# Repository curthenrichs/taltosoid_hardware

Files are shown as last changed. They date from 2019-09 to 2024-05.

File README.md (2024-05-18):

# taltosoid_srf
Taltos-oid seeks to understand the practicality in augmenting the human body with an additional robotic finger for everyday tasks. Taltos translates to shaman from Hungarian mythology. One potential defining trait of a shaman in the mythos is physical abnormalities such as an additional finger. Ergo Taltos-oid is using robotics to create a shaman through robotics (or just to help stabilize coffee cups).

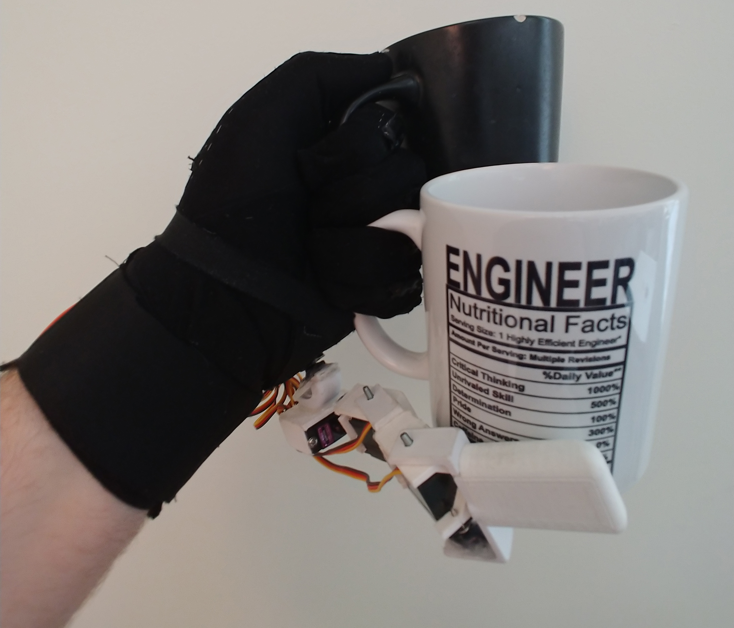
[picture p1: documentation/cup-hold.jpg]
Picture shows a gloved hand holding a cup with thumb, index finger, and middle finger. A second cup is being held with the ring finger, pinky, and the supernumerary robotic opposable finger


## Motivation
I have been fascinated with augmenting the human body with robotic limbs for years now. Nearly as long as I have been introduced to the concepts of transhumanism and post-humanism. There is something captivating about the question "what would be different about me if I were not human". My first attempt at extending human ability is to develop a supernumerary robotic finger that can be used to assist and augment the wearer in grasping tasks during daily living.

There are two schools of thought regarding the "agent-status" of the robotic finger. One view is to treat the robotic finger as a pass-through device extracting signals from EMG or finger tracking without any cognitive processes performed by the finger. This system relies on expertise of the wearer to control the device for the given task. The alternate view is to endow decision making onto the finger, in effect treating it as a traditional robotic agent and thus casting the control problem as social human-robot collaboration. I believe the second view is where the most impact with such a device can be found. (This project will explore both since the first view is much easier to get started with).

## Design
I aim to capture the general hardware and software decisions made. Each section will break down the discussion by version (at this time only version one).

### Hardware

#### Version One
The hardware design can be broken into three subsystems:
- Robotic Finger
- Resistive Sense Glove
- Controller Wrist Strap

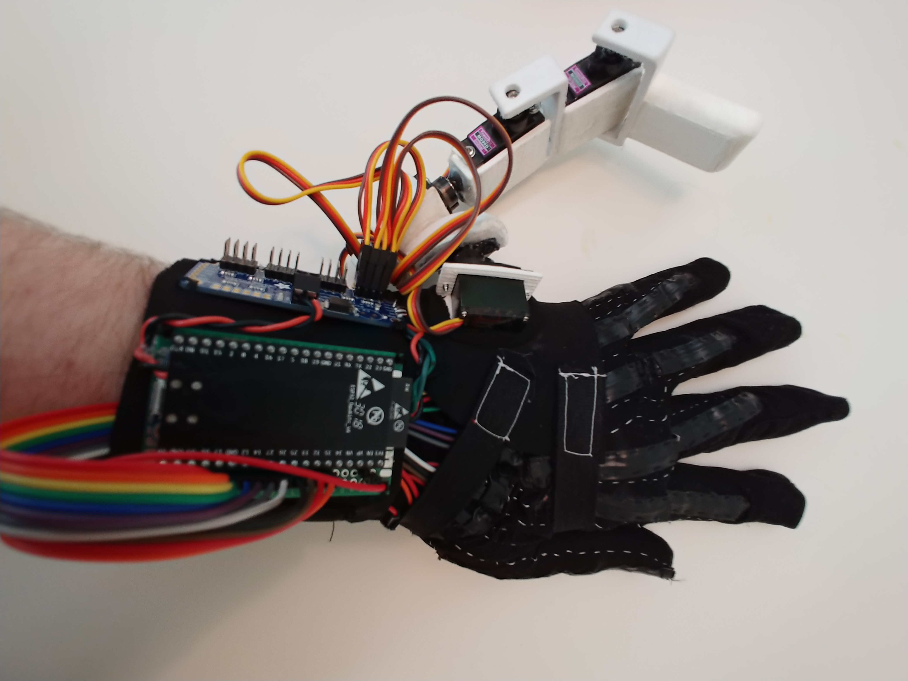
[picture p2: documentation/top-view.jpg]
Picture shows a gloved hand with the robotic finger attached. Control board (ESP32) is also shown. Version one hardware


**Robotic Finger**:
I designed a 3D printed robotic finger that uses high-torque micro servos to direct drive the joints. This design was primarily done for proof of concept. I suggest that future versions use some kind of linkage in order to keep the weight of the finger at the base. As it currently is, the servos don't have enough torque to hold even medium weighted objects. 

**Resistive Sense Glove**:
For version one I went with a simple-direct control strategy. In order to accomplish this I developed home-made flex sensors and sewed them onto a glove-liner. The sensors were made from two thick conductive threads with flexible resisitive material in between. I then used conductive copper fabric on each end as connective tabs. I covered the copper with conductive paint to adhere the conductive thread with the copper. Lastly, I sewwed thinner conductive thread down the glove to headerpins, again adhering with conductive paint and electrical tape. 

I later discovered while using the glove that sweat breaks down the conductive paint causing intermittent connections. I suggest future designs not use the approach described above. Instead it will be much more reliable to use off-the-shelf flex sensors even if they are less comfortable to wear. 

**Controller Wrist Strap**:
I build the controller wrist strap to physically keep the glove and finger aligned. Specifically, the wrist strap limits the glove from shifting around whent the user is moving their hand. Unfortuntely this makes it a bit uncomfortable to wear as it can get rather tight.

Electronically, the finger servos connect into a servo control board and the resistive sensors connect into an analog mux. The brains of the system is an ESP32 with arduino firmware. I also mounted an IMU at one point though later removed it for a different project.

**Improvement**:
Below are some of the key improvements needed for version two:

- Improved power system
- Custom, compact controller PCB
- Higher torque, more compact finger design

### Software

#### Version One
Version one software has a PC component and the low-level firmware. The PC was responsible for training and executing an ML model that mapped finger flex sensor input into appropriate joint control. The firmware acted as a relay. It captured low-level ADC voltage readings from the flex sensors. It provided direct joint-control to each joint. And it provided IMU readings. Communication was done over WiFi (thanks to the ESP32's capabilities).

I also started developing a ROS layer for this device, partially as a learning exercise and equally as the next step of building verison two. My goal is to build out several control strategies in simulation while working on a good second finger design.

Below are some of the key improvements needed for version two:

- Explore alternative methods for user control (EMG, nIRS, Vision)
- Communication from finger back to wearer (haptic?, animation?)
- Environment sensing (3D grasp targeting)
- Collision avoidance, context aware pose
- Augmentaton control strategies
- (Recently added) LLM control
- Tamagotchi mode

## Experiments
My goal once I develop version two is to perform a day-long autobiographical study wearing the finger. Work can also be done under more strict laboratory experiments investigating grasping tasks.

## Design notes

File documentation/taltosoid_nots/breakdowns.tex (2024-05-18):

I put my finger on today as I am restarting the project and wanted to remind myself of the wearability. First as I type, my wrist  wrests awkwardly, this is due to the mounting point of the finger. Second blood circulation at my thumb and index finger are not great due to the mounting Velcro straps to hold the flex sensors. The sensors themselves dig into my skin at the finger tips and at the base. Most prominent is the digging in on the index finger. As I wear the device the compute strap has a wire under that digs in as well. 

The finger mounting point is awkward to type on a keyboard and the sensor mounting makes it awkward to type on a phone. Taking pictures of the hand is also difficult. 

I am also not pleased with the Velcro finger straps removing sensation on the finger tips (often the straps make contact with the grasped object first). I also am not a fan of the open wires (and more generally the bulk) of the compute module on the wrist. Note too that this is without batter which adds considerable weight. 

The finger itself is worn and would need considerable rework if I go that route. I advise we continue to use the current finger, but rethink the control electronics.

What is my budget for this? \$ 100 for version 1.2. + the a couple hundred for version 2?

I think we ought to make a new glove thing and rework the current compute module for version 1.2. The underlying hardware is probably fine for an early evaluation provided I fix the comfort issues. Version 2 should have a better scheme for mounting the finger.

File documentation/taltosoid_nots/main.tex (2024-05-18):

%%%%%%%%%%%%%%%%%%%%%%%%%%%%%%%%%%%%%%%%%%%%%%%%%%%%%%%%%%%%%%%%%%%%%%%%%%%%%%%%
%2345678901234567890123456789012345678901234567890123456789012345678901234567890
%        1         2         3         4         5         6         7         8

\documentclass[letterpaper, 10 pt, conference]{ieeeconf}  % Comment this line out if you need a4paper

%\documentclass[a4paper, 10pt, conference]{ieeeconf}      % Use this line for a4 paper

\IEEEoverridecommandlockouts                              % This command is only needed if 
                                                          % you want to use the \thanks command

\overrideIEEEmargins                                      % Needed to meet printer requirements.

%In case you encounter the following error:
%Error 1010 The PDF file may be corrupt (unable to open PDF file) OR
%Error 1000 An error occurred while parsing a contents stream. Unable to analyze the PDF file.
%This is a known problem with pdfLaTeX conversion filter. The file cannot be opened with acrobat reader
%Please use one of the alternatives below to circumvent this error by uncommenting one or the other
%\pdfobjcompresslevel=0
%\pdfminorversion=4

% See the \addtolength command later in the file to balance the column lengths
% on the last page of the document

% The following packages can be found on http:\\www.ctan.org
%\usepackage{graphics} % for pdf, bitmapped graphics files
%\usepackage{epsfig} % for postscript graphics files
%\usepackage{mathptmx} % assumes new font selection scheme installed
%\usepackage{times} % assumes new font selection scheme installed
%\usepackage{amsmath} % assumes amsmath package installed
%\usepackage{amssymb}  % assumes amsmath package installed

\begin{document}

\title{\LARGE \bf Exploration of a Wearable Supernumerary Finger as Embodied Robotic Companion: An Autobiographical Case Study}

\author{Curt Henrichs}

% My goal is to write a short (4-page) paper regarding this topic

\maketitle
\thispagestyle{empty}
\pagestyle{empty}

\begin{abstract}

\end{abstract}

\section{Introduction}

The relationship between an agent and its environment informs both form(s) and function(s) it takes. Agents able to successfully operate within their environment have a high "fitness". For robotics, designers often have to consider the degree of structure provided within the environment; the proximity and relationship with humans the robot may encounter; and the task/role the it ought to perform. In human-robot interaction scenarios, a "fit" robot is often one that can successfully navigate the vagaries of human behavior. 

Wearable robots pose an interesting space to explore this "fitness" design task. Most prominently, wearable robots exist within the intimate social zone of their wearer during use and thus are enmeshed within the lives of their wearer. For example, this affords the robot access to observe and act during social interactions between the wearer and third-party agents. The designer also needs to consider casting the wearable agent as independent versus an extension of the wearer. This choice informs the set of behaviors a robot ought to perform. A wearer will expect independent behavior from a wearable tele-presence robot, but less so a prosthetic. The environments that a wearable robot will find itself in is as unstructured as the human wearer's. This could pose challenges if the robot's goal requires recognizing and manipulating objects with an end-effector. Even the proper mounting of wearable robots on the wearer's body during manipulation poses challenges to the designer.

In this paper, we focus on a specific subset of wearable robotics used to augment hand functionality, called supernumerary robotic fingers\footnote{Part of the broader set of supernumerary robotic limbs.}. We built a prototype system--\textit{Taltosoid}--designed to act as an embodied, artificial pet; inspired by popularized virtual pets (e.g., Tamagotchis). This work aims to explore the design of such a system. We discuss our findings through several self-experimentation case studies culminating with a proposal on future directions necessary to develop a robust taxonomy of the design space.

Our contributions are:
\begin{itemize}
    \item Design and implementation of a prototype embodied, artificial pet supernumerary robotic finger (\textit{Taltosoid});
    \item Case studies exploring usability and functionality of \textit{Taltosoid} through self-experimentation.
\end{itemize}

\section{Background}

\subsection{Supernumerary Fingers}

\subsection{Robot Companions}

\subsection{Design Space}

% Introduce Taltosoid here

\section{Method \& Design}
To design a compelling interaction between the wearer and finger, we conducted a preliminary autobiographical evaluation. The purpose of this evaluation is to understand what the wearer's common activities are and capture initial breakdowns whilst wearing the hardware. We then designed an embodied companion system running on the hardware. We showcase the functionality of the companion with several formative case studies drawn from a day-long autobiographical session. See each subsection for further discussion.

\subsection{Day in the Life of a Wearer}
Our goal is to understand a wearer's common activities--specifically how they use their hands---throughout a typical day. Furthermore, we want to capture the long-term use breakdowns of the current hardware prototype. This necessitates intrusive entry into the life of the wearer. Hence, we opt for an autobiographical design approach were researchers are framed as the the target user; thus performing the evaluation. We discuss the literature and limitations of this approach in the discussion section. The researcher (we) performed a two-day evaluation, with day one dedicated to tracking typical hand use and day two focused on wearing a supernumerary robotic finger in a limited actuation mode. 

During the day, we wore a camera mounted on the left shoulder facing forward and down to capture a top-down view of the activities. We also mounted a camera on our lower arm to further capture hand activity. For day two we also wore the hardware in a limited actuation mode. In this mode, the device used two flex sensors mounted on the researchers index finger and thumb to guide thumb position using a simple heuristic. 

The evaluation day was considered started after we started recording. We started wearing the cameras as soon as we woke up. The day ended when we went to bed; stopping recording and taking off the cameras. During the day, when a camera's battery became critically low, we would stop recording and switch out batteries. We did not consider this part of ``daily-life activities'' and thus disregard it from coding and analysis.

All video data was then coded for hand activity themes and wearability breakdowns following a grounded theory approach. After the 

\textit{Day One - A typical day -}

\textit{Day Two - Wearing the prototype -}

% Purpose is to understand the weare's common activites and capture initial breakdowns

\subsection{Designing the Embodied Companion}

\subsection{Case Studies}
Following the same protocol as our first evaluation, we performed a day-long usability evaluation of the hardware + embodied companion. We wore cameras on both the shoulder and lower arm. We coded the video data for hand activity and wearability breakdowns. 

\textit{Day Three - Wearing the companion - }

\subsubsection{Case 1}

\subsubsection{Case 2}

\subsubsection{Case 3}

\section{Discussion}

% autobiographical research, the good/bad/and ugly

\end{document}

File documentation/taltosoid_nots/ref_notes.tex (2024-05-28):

\section{Notes}

Why is situating a robot onto the human body an interesting and worthwhile project to explore?
- Passive vs active agent problem
    - Smart prosthetic are effectively passive agents mapping human input directly to an actuation state.
    - A social robot is an active agent separate from the self. We ascribe it motive and observe its actuation. 
    - Wearable robots could blend the line between these switching between active and passive robot states
- Robots situated on the human body live near-exclusively in the intimate social zone while in operation.
    - As such we expect interesting social breakdowns (if we cast this an active agent problem)
        - When should the robot engage in an activity? 
    - Do we gender the robot (and what are the users preferences there). Do we explore the sexual orientation of the robotic finger (if again treated as a multi-agent problem)
- Situated on the body offers access to the life of the user as they perform daily tasks
    - More importantly it affords affecting state in addition to gathering it
    - Cell-phones and wearables like smart bands/watches and eye wear approach this. It resolves the sensing (and in a limited case actuation ~ Holograms).
- How do these devices effect lifestyle e.g., clothing choice (style-design and accommodations). 
    - Would users be interested in making these modifications for an external agent
- Future is trans-human?

********* Human-robot proxemics: physical and psychological distancing in human-robot interaction - https://dl.acm.org/doi/abs/10.1145/1957656.1957786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

Persuasive Robotics: The influence of robot gender on human behavior - https://ieeexplore.ieee.org/document/5354116

Why Not Marry a Robot? - https://link.springer.com/chapter/10.1007/978-3-319-57738-8_1

Gendering Humanoid Robots: Robo-Sexism in Japan - https://journals.sagepub.com/doi/abs/10.1177/1357034x10364767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

Can you Tell the Robot by the Voice? An Exploratory Study on the Role of Voice in the Perception of Robots - https://ieeexplore.ieee.org/abstract/document/8673305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

Gendered robot voices influencing trust -
towards a robot recommendation system
 - https://webapps.cs.umu.se/uminf/reports/2020/001/part1.pdf#page=7

‘Robot Kung fu’: Gender and professional identity in biology and philosophy reviews - https://www.sciencedirect.com/science/article/abs/pii/S0378216607000161

Gendered voice and robot entities: Perceptions and reactions of male and female subjects - https://ieeexplore.ieee.org/abstract/document/5354204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

Is Your Roomba Male or Female? The Role of Gender Stereotypes and Cultural Norms in Robot Design - https://ojs.stanford.edu/ojs/index.php/intersect/article/view/171

The Philosophical Case for Robot Friendship - https://www.jstor.org/stable/10.5325/jpoststud.3.1.0005

When stereotypes meet robots: The double-edge sword of robot gender and personality in human–robot interaction - https://www.sciencedirect.com/science/article/pii/S0747563214002921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

Why supernumarary robotic fingers? What benefits to society does this confer? 

How do we gamify the pet finger process - (and why)? 
- Voluntary compliance / building habits (wearable fingers are not a well understood phenomena for the average wearer)
- Long-term study potential

Does Gamification Work? -- A Literature Review of Empirical Studies on Gamification - https://ieeexplore.ieee.org/abstract/document/6758978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

Tamagotchis need not die — Verification of statemate designs - https://link.springer.com/chapter/10.1007/BFb0054174

Virtual Pet Game Application to Train and Manage How to Raise a Cat Well and Properly - https://ieeexplore.ieee.org/abstract/document/9339682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

Disposable Love: The Rise and Fall of a Virtual Pet - https://journals.sagepub.com/doi/abs/10.1177/14614449922225591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

3D Virtual Pet Multiplayer Game Dengan Menggunakan Google Cardboard - https://repository.its.ac.id/75819/

Virtual Pet: Trends of Development - https://link.springer.com/chapter/10.1007/978-3-030-37737-3_47

Bouncy: An Interactive Life-Like Pet - https://citeseerx.ist.psu.edu/viewdoc/download?doi=10.1.1.24.6293&rep=rep1&type=pdf

Design and implementation of an educational virtual pet using the OCC theory - https://link.springer.com/article/10.1007/s12652-011-0089-4

A study of integrating social networking service into the virtual pet web game system - https://ieeexplore.ieee.org/abstract/document/6765475

Developing a believable interactive agent using
virtual pet design - http://tombattey.com/wp-content/uploads/2019/09/Developing-a-believable-interactive-agent-using-virtual-pet-design.pdf

Pretty Pelvis: A Virtual Pet Application That Breaks Sedentary Time by Promoting Gestural Interaction - https://dl.acm.org/doi/abs/10.1145/2702613.2732807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

AIBO: Toward the Era of Digital Creatures - https://journals.sagepub.com/doi/abs/10.1177/02783640122068092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

Loving a virtual pet: Steps toward the technological erosion of emotion - https://www.proquest.com/docview/200590681?pq-origsite=gscholar&fromopenview=true

Methodology
A Self-Guiding Tool to Conduct Research With Embodiment Technologies Responsibly - https://internal-journal.frontiersin.org/articles/10.3389/frobt.2020.00022/full

self-experimentation / autobiographical

Revealing Tensions in Autobiographical Design in HCI - https://dl.acm.org/doi/abs/10.1145/3196709.3196781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

Autobiographical design in HCI research: designing and learning through use-it-yourself - https://dl.acm.org/doi/abs/10.1145/2317956.2318034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

A Sample of One: First-Person Research Methods in HCI - https://dl.acm.org/doi/abs/10.1145/3301019.3319996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

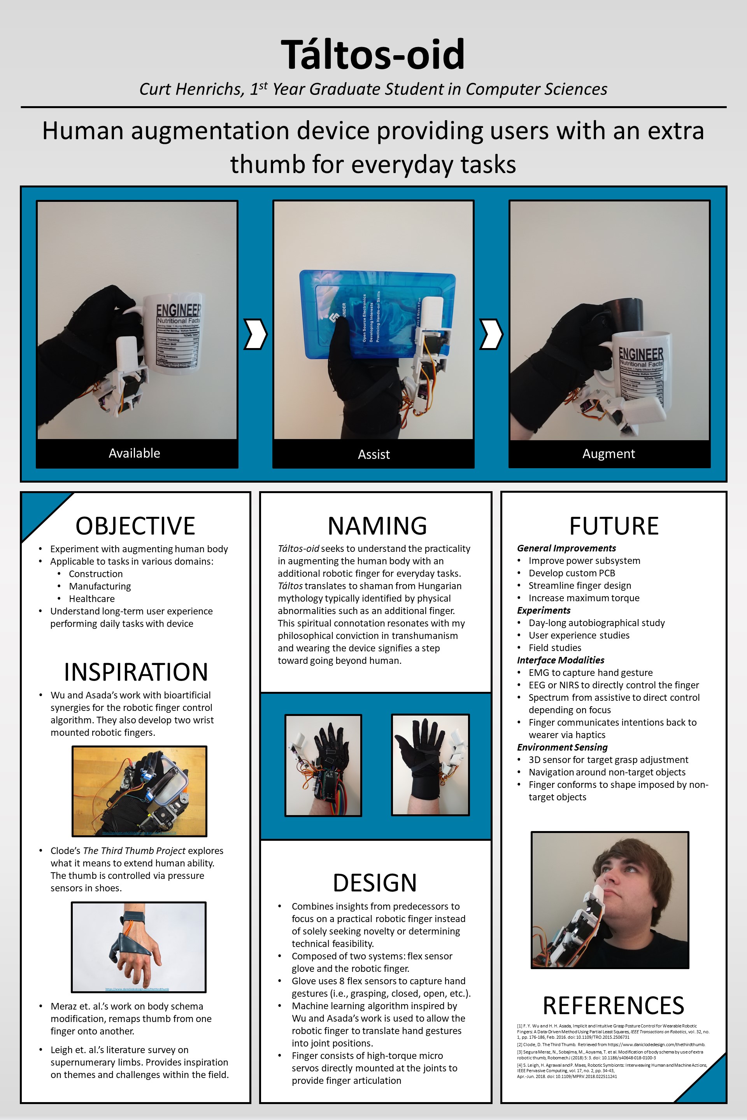
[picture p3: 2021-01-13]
documentation/Poster.jpg

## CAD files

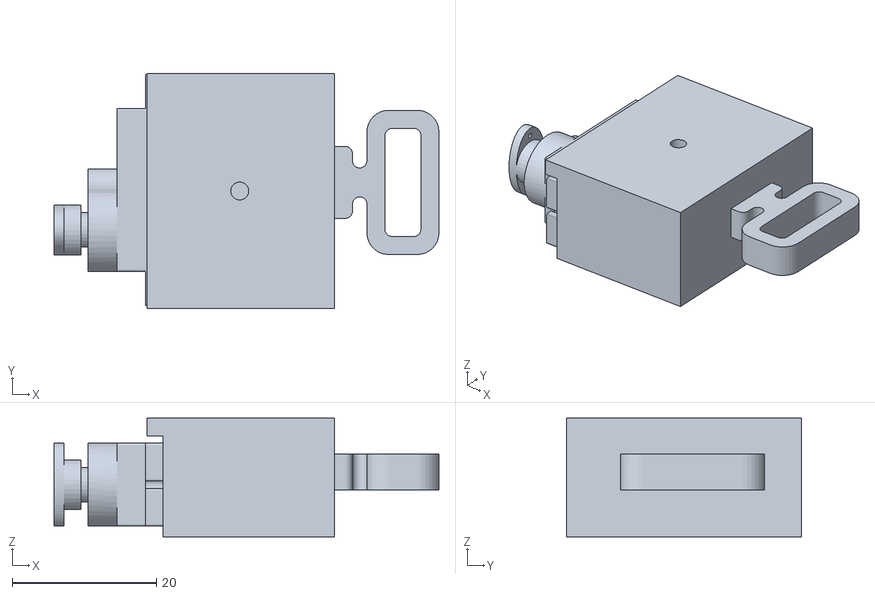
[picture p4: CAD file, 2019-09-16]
taltosoid_driver/description/meshes/rotation_root.stl
53.4 x 32.6 x 16.5

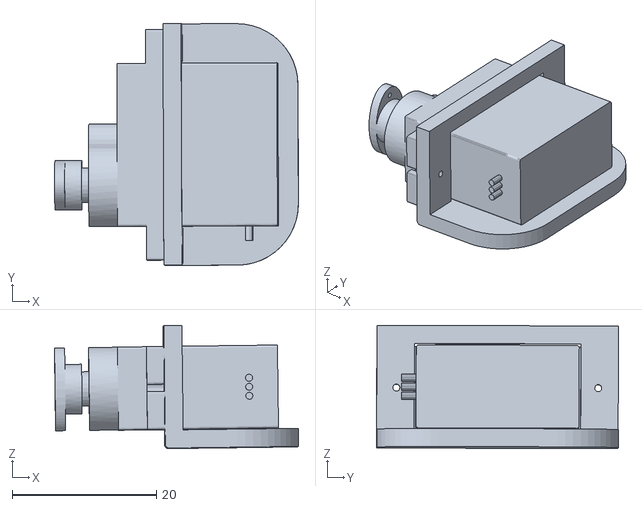
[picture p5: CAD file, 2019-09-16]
taltosoid_driver/description/meshes/finger_root.stl
33.9 x 33.6 x 17.1

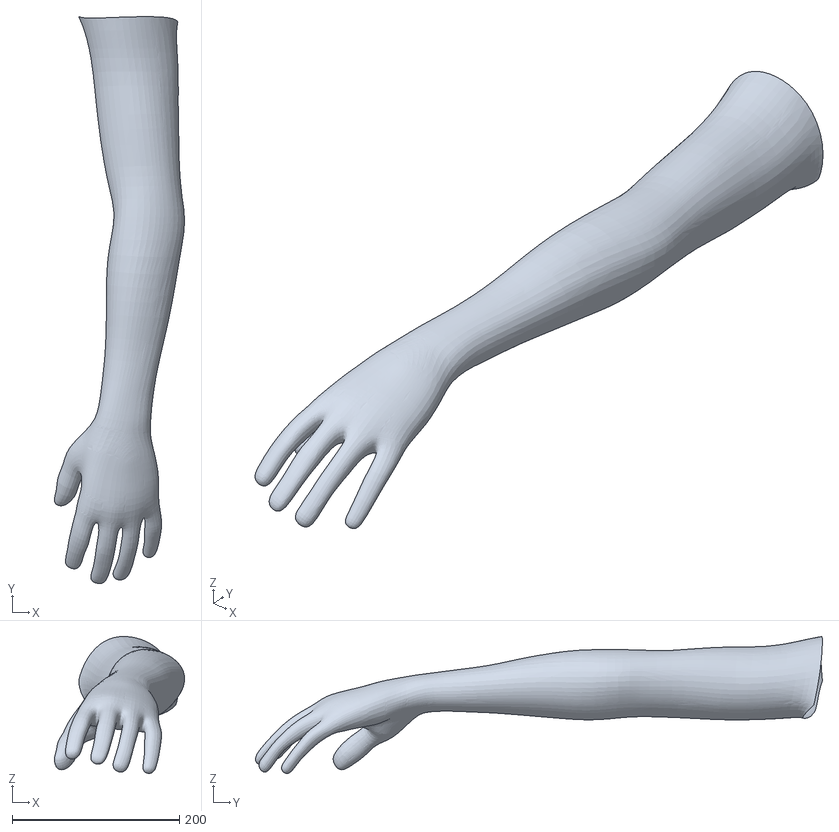
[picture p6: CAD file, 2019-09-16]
taltosoid_driver/description/meshes/hand.stl
155.7 x 678.1 x 163.9

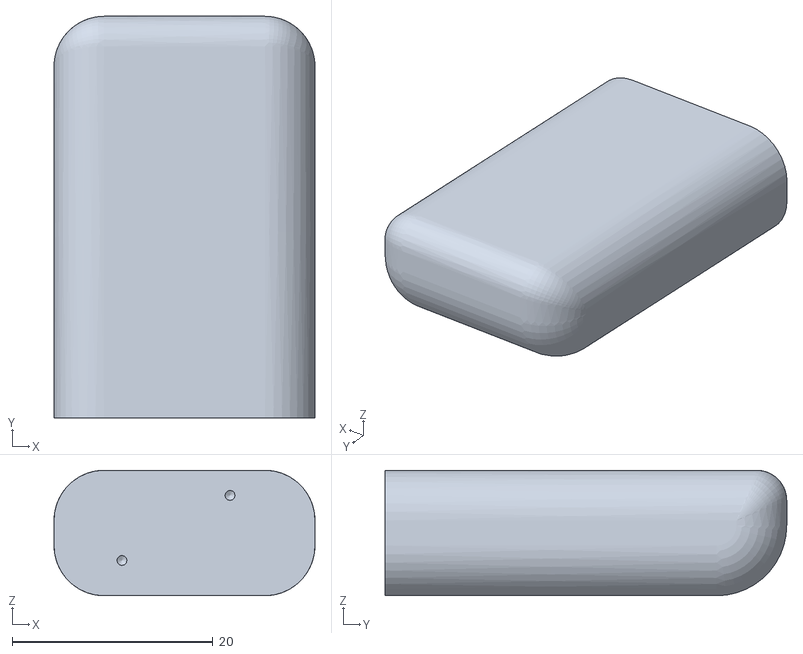
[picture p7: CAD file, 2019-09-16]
taltosoid_driver/description/meshes/finger_tip.stl
26.0 x 40.0 x 12.5

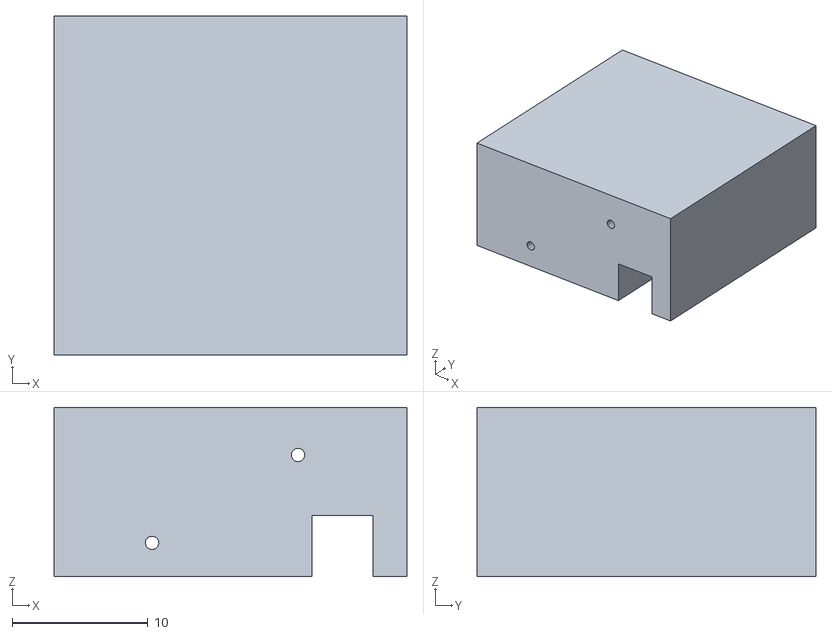
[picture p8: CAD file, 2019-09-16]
taltosoid_driver/description/meshes/spacer.stl
26.0 x 25.0 x 12.5

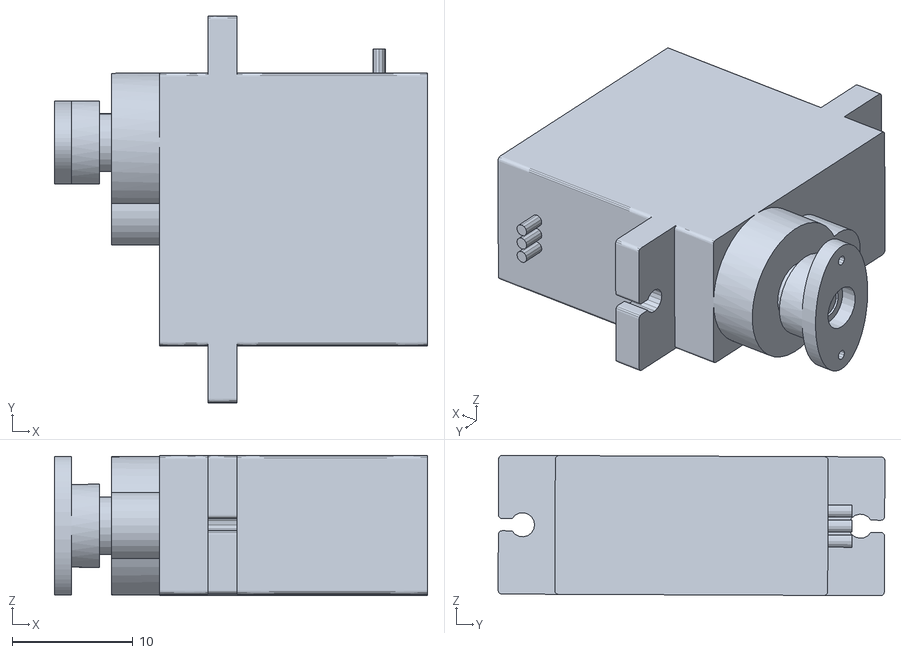
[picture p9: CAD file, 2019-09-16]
taltosoid_driver/description/meshes/servo.stl
30.9 x 32.1 x 11.6

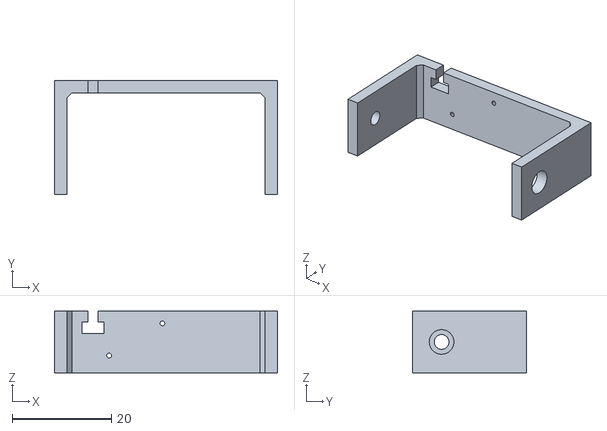
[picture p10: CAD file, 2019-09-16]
taltosoid_driver/description/meshes/finger_hinge.stl
45.0 x 23.0 x 12.5

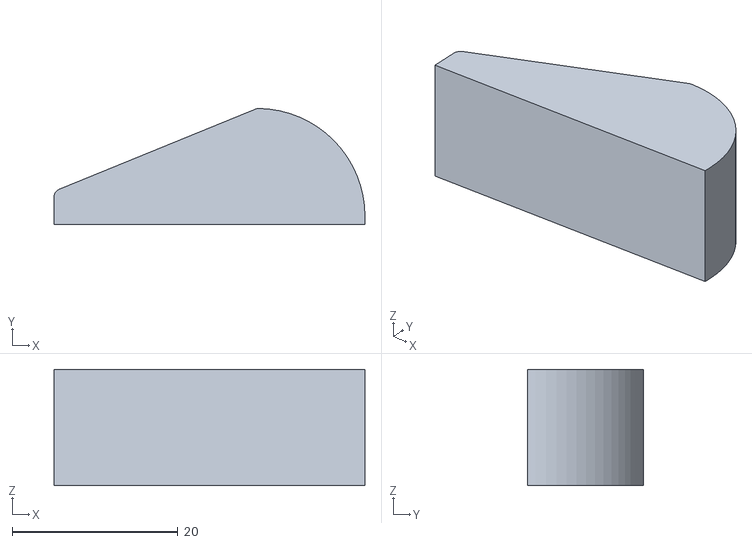
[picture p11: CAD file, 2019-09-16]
taltosoid_driver/description/meshes/base_spacer.stl
37.5 x 14.0 x 14.0

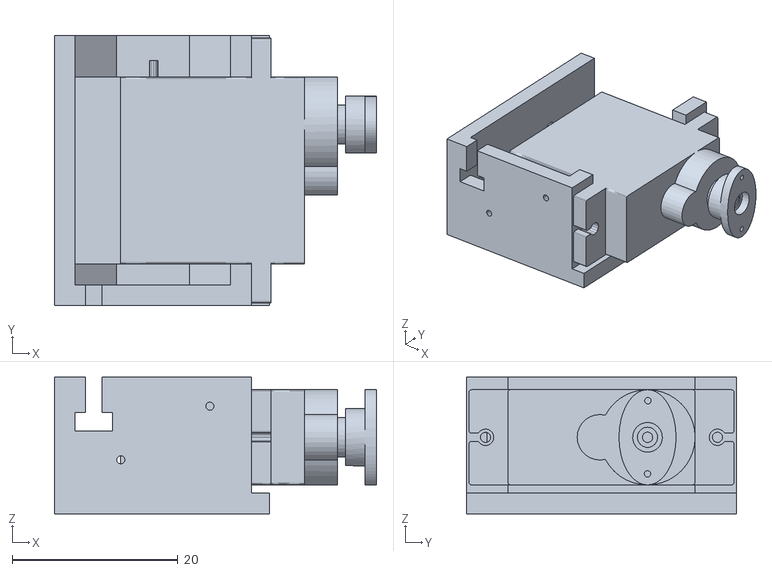
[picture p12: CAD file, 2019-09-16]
taltosoid_driver/description/meshes/finger_segment.stl
38.9 x 32.6 x 16.5

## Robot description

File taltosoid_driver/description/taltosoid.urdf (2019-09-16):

<?xml version="1.0"?>
<robot name="">

  <link name="world"/>
  <link name="base_link">
    <!--
    <visual>
      <origin rpy="0 0 0" xyz="0 0 -0.01"/>
      <geometry>
        <cylinder length="0.01" radius="0.05"/>
      </geometry>
    </visual>
    -->
  </link>

  <link name="finger_root">
    <visual>
      <origin rpy="0 0 0" xyz="0 0 0"/>
      <geometry>
        <mesh filename="package://taltosoid_hardware/description/meshes/finger_root.stl" scale="0.001 0.001 0.001"/>
      </geometry>
    </visual>
    <collision>
      <origin rpy="0 0 0" xyz="0 0 0"/>
      <geometry>
        <mesh filename="package://taltosoid_hardware/description/meshes/finger_root.stl" scale="0.001 0.001 0.001"/>
      </geometry>
    </collision>
  </link>

  <link name="base_spacer">
    <visual>
      <origin rpy="-1.57 1.57 0" xyz="0 -0.007 0.0275"/>
      <geometry>
        <mesh filename="package://taltosoid_hardware/description/meshes/base_spacer.stl" scale="0.001 0.001 0.001"/>
      </geometry>
    </visual>
    <collision>
      <origin rpy="0 0 0" xyz="0 0 0"/>
      <geometry>
        <mesh filename="package://taltosoid_hardware/description/meshes/base_spacer.stl" scale="0.001 0.001 0.001"/>
      </geometry>
    </collision>
  </link>

  <link name="rotation_root">
    <visual>
      <origin rpy="0 -1.57 -3.14" xyz="0 0 0.001"/>
      <geometry>
        <mesh filename="package://taltosoid_hardware/description/meshes/rotation_root.stl" scale="0.001 0.001 0.001"/>
      </geometry>
    </visual>
    <collision>
      <origin rpy="0 -1.57 -3.14" xyz="0 0 0.001"/>
      <geometry>
        <mesh filename="package://taltosoid_hardware/description/meshes/rotation_root.stl" scale="0.001 0.001 0.001"/>
      </geometry>
    </collision>
  </link>

  <link name="finger_segment_1">
    <visual>
      <origin rpy="-1.57 0 1.57" xyz="0 0.001 0"/>
      <geometry>
        <mesh filename="package://taltosoid_hardware/description/meshes/finger_segment.stl" scale="0.001 0.001 0.001"/>
      </geometry>
    </visual>
    <collision>
      <origin rpy="-1.57 0 1.57" xyz="0 0.001 0"/>
      <geometry>
        <mesh filename="package://taltosoid_hardware/description/meshes/finger_segment.stl" scale="0.001 0.001 0.001"/>
      </geometry>
    </collision>
  </link>

  <link name="finger_hinge_1">
    <visual>
      <origin rpy="-1.57 0 1.57" xyz="0 0.001 -0.0055"/>
      <geometry>
        <mesh filename="package://taltosoid_hardware/description/meshes/finger_hinge.stl" scale="0.001 0.001 0.001"/>
      </geometry>
    </visual>
    <collision>
      <origin rpy="-1.57 0 1.57" xyz="0 0.001 -0.0055"/>
      <geometry>
        <mesh filename="package://taltosoid_hardware/description/meshes/finger_hinge.stl" scale="0.001 0.001 0.001"/>
      </geometry>
    </collision>
  </link>

  <link name="finger_segment_2">
    <visual>
      <origin rpy="-1.57 0 1.57" xyz="0 0.001 0"/>
      <geometry>
        <mesh filename="package://taltosoid_hardware/description/meshes/finger_segment.stl" scale="0.001 0.001 0.001"/>
      </geometry>
    </visual>
    <collision>
      <origin rpy="-1.57 0 1.57" xyz="0 0.001 0"/>
      <geometry>
        <mesh filename="package://taltosoid_hardware/description/meshes/finger_segment.stl" scale="0.001 0.001 0.001"/>
      </geometry>
    </collision>
  </link>

  <link name="finger_hinge_2">
    <visual>
      <origin rpy="-1.57 0 1.57" xyz="0 0.001 -0.0055"/>
      <geometry>
        <mesh filename="package://taltosoid_hardware/description/meshes/finger_hinge.stl" scale="0.001 0.001 0.001"/>
      </geometry>
    </visual>
    <collision>
      <origin rpy="-1.57 0 1.57" xyz="0 0.001 -0.0055"/>
      <geometry>
        <mesh filename="package://taltosoid_hardware/description/meshes/finger_hinge.stl" scale="0.001 0.001 0.001"/>
      </geometry>
    </collision>
  </link>

  <link name="finger_tip">
    <visual>
      <origin rpy="-1.57 0 1.57" xyz="0 0.001 -0.0055"/>
      <geometry>
        <mesh filename="package://taltosoid_hardware/description/meshes/finger_tip.stl" scale="0.001 0.001 0.001"/>
      </geometry>
    </visual>
    <collision>
      <origin rpy="-1.57 0 1.57" xyz="0 0.001 -0.0055"/>
      <geometry>
        <mesh filename="package://taltosoid_hardware/description/meshes/finger_tip.stl" scale="0.001 0.001 0.001"/>
      </geometry>
    </collision>
  </link>

  <link name="ee_target">
    <visual>
      <origin rpy="0 0 0" xyz="0 0 -0.015"/>
      <geometry>
         <sphere radius="0.01"/>
      </geometry>
      <material name="green">
            <color rgba="0 1 0 0.33"/>
      </material>
    </visual>
  </link>


  <joint name="world_to_base_link" type="fixed">
    <parent link="world"/>
    <child link="base_link"/>
    <origin xyz="0 0 0"/>
  </joint>

  <joint name="base_link_to_finger_root" type="fixed">
    <parent link="base_link"/>
    <child link="finger_root"/>
    <origin xyz="0 0 0"/>
  </joint>

  <joint name="finger_root_to_base_spacer" type="revolute">
    <parent link="finger_root"/>
    <child link="base_spacer"/>

    <axis xyz="1 0 0"/>
    <limit effort="1000.0" lower="-1.57" upper="1.57" velocity="0.5"/>
    <origin rpy="1.57 0 0" xyz="-0.017 -0.00565 -0.00035"/>
  </joint>


  <joint name="base_spacer_to_rotation_root" type="fixed">
    <parent link="base_spacer"/>
    <child link="rotation_root"/>
    <origin rpy="0 0.4 0" xyz="-0.016 0 0.02"/>
  </joint>

  <joint name="rotation_root_to_finger_segment_1" type="revolute">
    <parent link="rotation_root"/>
    <child link="finger_segment_1"/>

    <axis xyz="0 0 1"/>
    <limit effort="1000.0" lower="-1.57" upper="1.57" velocity="0.5"/>
    <origin rpy="0 0 0" xyz="-0.001 0.0055 -0.042"/>
  </joint>

  <joint name="finger_segment_1_to_finger_hinge_1" type="revolute">
    <parent link="finger_segment_1"/>
    <child link="finger_hinge_1"/>

    <axis xyz="0 1 0"/>
    <limit effort="1000.0" lower="-1.57" upper="1.57" velocity="0.5"/>
    <origin rpy="0 0 0" xyz="-0.001 0 -0.0055"/>
  </joint>

  <joint name="finger_hinge_1_to_finger_segment_2" type="fixed">
    <parent link="finger_hinge_1"/>
    <child link="finger_segment_2"/>
    <origin xyz="0 0 -0.0333"/>
  </joint>

  <joint name="finger_segment_2_to_finger_hinge_2" type="revolute">
    <parent link="finger_segment_2"/>
    <child link="finger_hinge_2"/>

    <axis xyz="0 1 0"/>
    <limit effort="1000.0" lower="-1.57" upper="1.57" velocity="0.5"/>
    <origin rpy="0 0 0" xyz="-0.001 0 -0.0055"/>
  </joint>

  <joint name="finger_hinge_2_to_finger_tip" type="fixed">
    <parent link="finger_hinge_2"/>
    <child link="finger_tip"/>
    <origin xyz="0 -0.011 -0.0315"/>
  </joint>

  <joint name="finger_tip_to_ee_target" type="fixed">
    <parent link="finger_tip"/>
    <child link="ee_target"/>
    <origin xyz="0 0.006 -0.006"/>
  </joint>

</robot>

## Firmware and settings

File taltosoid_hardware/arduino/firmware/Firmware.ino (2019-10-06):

/**
 * Supernumerary Robotic Finger
 * Version 1.1.5
 * @author Curt Henrichs
 * @date 4-19-19
 *
 * Firmware (main) file.
 */

//==============================================================================
//  Libraries
//==============================================================================

#include "HardwareConfig.h"
#include "FingerDriver.h"
#include "FlexSensors.h"

#include <ArduinoJson.h>
#include <elapsedMillis.h>

//==============================================================================
//  Constants and Macro Definitions
//==============================================================================

#define API_RX_BUFFER_SIZE (250)

#define API_MSG_DELIMITER '\0'

#define FLEX_SENSOR_SAMPLE_TIMER_THRESHOLD (50)
#define API_DATA_PUSH_TIMER (100)

#define SEND_JSON(json, device) do { serializeJson(json, device); device.print(API_MSG_DELIMITER); } while(0)

//==============================================================================
//  Private Data Members
//==============================================================================

static elapsedMillis flexSensorSampleTimer;
static elapsedMillis apiDataPushTimer;

static char _rx_buffer[API_RX_BUFFER_SIZE+1];
static int _rx_buffer_index = 0;
static bool _rx_buffer_contains_msg = false;

//==============================================================================
//  Private Function Prototypes
//==============================================================================

static void _api_push_msg(void);
static void _api_handle_set_joint_request(int id, int angle);
static void _api_handle_get_joint_request(int id);
static void _api_handle_flex_sensor_request(int id);
static void _api_handle_metadata_request(void);

static char* _sensor_index_to_id_str(int index);
static int _sensor_id_str_to_index(const char* str);
static char* _joint_index_to_id_str(int index);
static int _joint_id_str_to_index(const char* str);

static bool firstIteration = true;

//==============================================================================
//  Main
//==============================================================================

void setup(void) {
  flexSensorSampleTimer = 0;
  apiDataPushTimer = 0;

  _rx_buffer[API_RX_BUFFER_SIZE] = '\0';
  _rx_buffer_index = 0;
  _rx_buffer_contains_msg = false;

  hw_init();
  fd_init();
}

void loop(void) {

  // On first iteration, correct joints of finger
  if (firstIteration) {
    firstIteration = false;
    fd_reset_all_joint_states();
  }

  // process character string from serial, connected to external device
  while (API_SERIAL.available() && !_rx_buffer_contains_msg) {

    char c = API_SERIAL.read();

    if (c == API_MSG_DELIMITER) {
      _rx_buffer[_rx_buffer_index] = '\0';
      _rx_buffer_contains_msg = true;
    } else {
      _rx_buffer[_rx_buffer_index] = c;
    }
    _rx_buffer_index++;

    if (_rx_buffer_index >= API_RX_BUFFER_SIZE && !_rx_buffer_contains_msg) {
      _rx_buffer_index = 0;
    }
  }

  // handle API requests from external device
  if (_rx_buffer_contains_msg) {
    _rx_buffer_contains_msg = false;
    _rx_buffer_index = 0;

    // convert to JSON document
    StaticJsonDocument<300> rxDoc;
    deserializeJson(rxDoc,(const char*)(_rx_buffer));

    const char* requestType = rxDoc["request_type"];
    if (requestType != NULL) {
      if (strcmp(requestType,"joint_get") == 0) {
        int id = _joint_id_str_to_index(rxDoc["joint_id"]);
        _api_handle_get_joint_request(id);
      } else if (strcmp(rxDoc["request_type"],"joint_set") == 0) {
        int id = _joint_id_str_to_index(rxDoc["joint_id"]);
        if (rxDoc.containsKey("angle")) {
          int angle = rxDoc["angle"];
          _api_handle_set_joint_request(id,angle);
        } else {
          StaticJsonDocument<500> txDoc;
          txDoc["error"] = true;
          txDoc["error_msg"] = "missing 'angle' attribute";
          txDoc["buffer"] = _rx_buffer;
          SEND_JSON(txDoc, API_SERIAL);
        }
      } else if (strcmp(rxDoc["request_type"],"flex_sensor_get") == 0) {
        int id = _sensor_id_str_to_index(rxDoc["flex_id"]);
        _api_handle_flex_sensor_request(id);
      } else if (strcmp(rxDoc["request_type"],"metadata_get") == 0) {
        _api_handle_metadata_request();
      } else if (strcmp(rxDoc["request_type"],"force_push_msg") == 0) {
        _api_push_msg();
      } else {
        StaticJsonDocument<500> txDoc;
        txDoc["error"] = true;
        txDoc["error_msg"] = "invalid type";
        txDoc["buffer"] = _rx_buffer;
        SEND_JSON(txDoc, API_SERIAL);
      }
    } else{
      StaticJsonDocument<500> txDoc;
        txDoc["error"] = true;
        txDoc["error_msg"] = "request type not specified";
        txDoc["buffer"] = _rx_buffer;
        SEND_JSON(txDoc, API_SERIAL);
    }
  }

  // Sample sensors
  if (flexSensorSampleTimer >= FLEX_SENSOR_SAMPLE_TIMER_THRESHOLD) {
    flexSensorSampleTimer -= FLEX_SENSOR_SAMPLE_TIMER_THRESHOLD;
    fx_update();
  }

  // Push data to external device
  if (apiDataPushTimer >= API_DATA_PUSH_TIMER) {
    apiDataPushTimer -= API_DATA_PUSH_TIMER;
    _api_push_msg();
  }

  delay(10);
}

//==============================================================================
//  Private Function Implementation
//==============================================================================

static void _api_push_msg(void) {

  StaticJsonDocument<1000> doc;

  doc["message_type"] = "state_push";

  // read flex sensors
  for (int i=0; i<__NUM_FLEX_SENSORS__; i++) {
    doc[_sensor_index_to_id_str(i)] = fx_get((FlexSensorId_t)(i));
  }

  // read current joint states
  for (int i=0; i<__NUM_JOINTS__; i++) {
    doc[_joint_index_to_id_str(i)] = fd_get_joint_state((JointId_t)(i));
  }

  SEND_JSON(doc, API_SERIAL);
}

static void _api_handle_set_joint_request(int id, int angle) {

  StaticJsonDocument<100> doc;

  doc["joint_id"] = _joint_index_to_id_str(id);
  doc["result"] = fd_set_joint_state(((JointId_t)(id)),angle);

  SEND_JSON(doc, API_SERIAL);
}

static void _api_handle_get_joint_request(int id) {

  StaticJsonDocument<100> doc;

  doc["joint_id"] = _joint_index_to_id_str(id);
  doc["result"] = fd_get_joint_state((JointId_t)(id));

  SEND_JSON(doc, API_SERIAL);
}

static void _api_handle_flex_sensor_request(int id) {

  StaticJsonDocument<100> doc;

  doc["flex_id"] = _sensor_index_to_id_str(id);
  doc["result"] = fx_get(((FlexSensorId_t)(id)));

  SEND_JSON(doc, API_SERIAL);

}

static void _api_handle_metadata_request(void) {

  char chipIdStr[64];
  uint64_t chipid = ESP.getEfuseMac();
  sprintf(chipIdStr,"%04X%08X",(uint16_t)(chipid>>32),(uint32_t)(chipid));

  StaticJsonDocument<300> doc;

  doc["msg_type"] = "metadata";
  doc["chip_id"] = chipIdStr;
  doc["software_id"] = VERSION_STR;

  SEND_JSON(doc, API_SERIAL);
}

static char* _sensor_index_to_id_str(int index) {
  if (index == FLEX_0_0) {
    return "flex_0_0";
  } else if (index == FLEX_0_1) {
    return "flex_0_1";
  } else if (index == FLEX_1_0) {
    return "flex_1_0";
  } else if (index == FLEX_1_1) {
    return "flex_1_1";
  } else if (index == FLEX_2_0) {
    return "flex_2_0";
  } else if (index == FLEX_2_1) {
    return "flex_2_1";
  } else if (index == FLEX_3_0) {
    return "flex_3_0";
  } else if (index == FLEX_3_1) {
    return "flex_3_1";
  } else if (index == FLEX_4_0) {
    return "flex_4_0";
  } else if (index == FLEX_4_1) {
    return "flex_4_1";
  } else if (index == FLEX_5_0) {
    return "flex_5_0";
  } else if (index == FLEX_6_0) {
    return "flex_6_0";
  } else {
    return "invalid";
  }
}

static int _sensor_id_str_to_index(const char* str) {
  if (str != NULL) {
    if (strcmp(str,"flex_0_0") == 0) {
      return FLEX_0_0;
    } else if (strcmp(str,"flex_0_1") == 0) {
      return FLEX_0_1;
    } else if (strcmp(str,"flex_1_0") == 0) {
      return FLEX_1_0;
    } else if (strcmp(str,"flex_1_1") == 0) {
      return FLEX_1_1;
    } else if (strcmp(str,"flex_2_0") == 0) {
      return FLEX_2_0;
    } else if (strcmp(str,"flex_2_1") == 0) {
      return FLEX_2_1;
    } else if (strcmp(str,"flex_3_0") == 0) {
      return FLEX_3_0;
    } else if (strcmp(str,"flex_3_1") == 0) {
      return FLEX_3_1;
    } else if (strcmp(str,"flex_4_0") == 0) {
      return FLEX_4_0;
    } else if (strcmp(str,"flex_4_1") == 0) {
      return FLEX_4_1;
    } else if (strcmp(str,"flex_5_0") == 0) {
      return FLEX_5_0;
    } else if (strcmp(str,"flex_6_0") == 0) {
      return FLEX_6_0;
    } else {
      return -1;
    }
  } else {
    return -1;
  }
}

static char* _joint_index_to_id_str(int index) {
  if (index == JOINT_0) {
    return "joint_0";
  } else if (index == JOINT_1) {
    return "joint_1";
  } else if (index == JOINT_2) {
    return "joint_2";
  } else if (index == JOINT_3) {
    return "joint_3";
  } else {
    return "invalid";
  }
}

static int _joint_id_str_to_index(const char* str) {
  if (str != NULL) {
    if (strcmp(str,"joint_0") == 0) {
      return JOINT_0;
    } else if (strcmp(str,"joint_1") == 0) {
      return JOINT_1;
    } else if (strcmp(str,"joint_2") == 0) {
      return JOINT_2;
    } else if (strcmp(str,"joint_3") == 0) {
      return JOINT_3;
    } else {
      return -1;
    }
  } else {
    return -1;
  }
}

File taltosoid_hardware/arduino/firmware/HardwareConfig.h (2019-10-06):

/**
 * Supernumerary Robotic Finger
 * Version 1.1.5
 * @author Curt Henrichs
 * @date 4-19-19
 *
 * Hardware Configuration
 */

#ifndef HARDWARE_CONFIG_H
#define HARDWARE_CONFIG_H

//==============================================================================
//  Libraries
//==============================================================================

#include <Arduino.h>
#include <Wire.h>

#include "BluetoothSerial.h"

//==============================================================================
//  Control Flags
//==============================================================================

#define DEBUG_MODE (false)

//==============================================================================
//  Device Pinout
//==============================================================================

/*
#define FLEX_0_0_PIN (13)
#define FLEX_0_1_PIN (12)
#define FLEX_1_0_PIN (14)
#define FLEX_1_1_PIN (27)
#define FLEX_2_0_PIN (26)
#define FLEX_2_1_PIN (25)
#define FLEX_3_0_PIN (33)
#define FLEX_3_1_PIN (32)
#define FLEX_4_0_PIN (15)
#define FLEX_4_1_PIN (0)
#define FLEX_5_0_PIN (4)
#define FLEX_6_0_PIN (2)
*/

#define MUX_SIG_PIN (33)
#define MUX_S3_PIN (25)
#define MUX_S2_PIN (26)
#define MUX_S1_PIN (27)
#define MUX_S0_PIN (14)
#define MUX_EN_PIN (12)
#define MUX_VP_PIN (13)
#define MUX_VN_PIN (0)

#define I2C_SCL_PIN (22)
#define I2C_SDA_PIN (21)

//==============================================================================
//  Constants and Macro Definitions
//==============================================================================

#define DEBUG_SERIAL (Serial)
#define DEBUG_SERIAL_BAUD (115200)

extern const char* VERSION_STR;

extern BluetoothSerial SerialBT;
extern const char* BLUETOOTH_DEV_NAME;

#if DEBUG_MODE
#define API_SERIAL DEBUG_SERIAL
#else
#define API_SERIAL SerialBT
#endif

//==============================================================================
//  I2C Addresses
//==============================================================================

#define SERVO_DRIVER_ADDRESS (0x40)

//==============================================================================
//  Public Function Prototypes
//==============================================================================

void hw_init(void);

#endif

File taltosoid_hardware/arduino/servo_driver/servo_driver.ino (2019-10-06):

#include <Servo.h>

#define BASE_SERVO_PIN (6)
#define MID_SERVO_PIN (9)
#define TIP_SERVO_PIN (10)


// Servo bounds (degrees)
#define BASE_DEG_MIN (20)
#define BASE_DEG_MAX (170)
#define MID_DEG_MIN (55)
#define MID_DEG_MAX (170)
#define TIP_DEG_MIN (20)
#define TIP_DEG_MAX (170)

// Servo default state
#define BASE_DEG_DEFAULT (160)
#define MID_DEG_DEFAULT (140)
#define TIP_DEG_DEFAULT (90)


Servo baseServo;
Servo midServo;
Servo tipServo;

int baseServoValue;
int midServoValue;
int tipServoValue;

char buffer[64];

void setup() {
 Serial.begin(115200);

 baseServo.attach(BASE_SERVO_PIN);
 midServo.attach(MID_SERVO_PIN);
 tipServo.attach(TIP_SERVO_PIN);

 tipServo.write(TIP_DEG_DEFAULT);
 tipServoValue = TIP_DEG_DEFAULT;
 midServo.write(MID_DEG_DEFAULT);
 midServoValue = MID_DEG_DEFAULT;
 baseServo.write(BASE_DEG_DEFAULT);
 baseServoValue = BASE_DEG_DEFAULT;

 Serial.println("Setup Complete");
}

void loop() {

  // Capture serial data
  memset(buffer,0,64);
  int len = Serial.readBytesUntil('\n', buffer, 64);

  // Run CLI for servo driver
  if (len != 0) {
    int mode, servoId, value;
    if(sscanf(buffer,"%d:%d:%d",&mode,&servoId,&value) != 3) {
      // invalid format
      Serial.println("Invalid command form, use <'MODE'>:<'ID'>:<'VALUE'>");
    } else if (mode == 0) {
      if (servoId == 0) {
        if (boundCheck(value,BASE_DEG_MIN,BASE_DEG_MAX)) {
          baseServo.write(value);
          baseServoValue = value;
          Serial.print("Set Servo 0 to ");
          Serial.println(value);
        } else {
          Serial.println("Invalid bound for Servo 0");
        }
      } else if (servoId == 1) {
        if (boundCheck(value,MID_DEG_MIN,MID_DEG_MAX)) {
          midServo.write(value);
          midServoValue = value;
          Serial.print("Set Servo 1 to ");
          Serial.println(value);
        } else {
          Serial.println("Invalid bound for Servo 1");
        }
      } else if (servoId == 2) {
        if(boundCheck(value,TIP_DEG_MIN,TIP_DEG_MAX)) {
          tipServo.write(value);
          tipServoValue = value;
          Serial.print("Set Servo 2 to ");
          Serial.println(value);
        } else {
          Serial.println("Invalid bound for Servo 2");
        }
      } else {
        // invalid servo id
        Serial.println("Invalid Servo ID");
      }
    } else if (mode == 1) {
      if (servoId == 0) {
        Serial.print("Get Servo 0 ");
        Serial.println(baseServoValue);
      } else if (servoId == 1) {
        Serial.print("Get Servo 1 ");
        Serial.println(midServoValue);
      } else if (servoId == 2) {
        Serial.print("Get Servo 2 ");
        Serial.println(tipServoValue);
      } else {
        // invalid servo id
        Serial.println("Invalid Servo ID");
      }
    } else {
      //invalid mode
      Serial.println("Invalid Mode");
    }
  }

  delay(50);

}

bool boundCheck(int value, int min, int max) {
  return value >= min && value <= max;
}

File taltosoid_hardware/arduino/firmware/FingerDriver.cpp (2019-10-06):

/**
 * Supernumerary Robotic Finger
 * Version 1.1.5
 * @author Curt Henrichs
 * @date 4-19-19
 *
 * Robotic Finger Joint Driver
 */

//==============================================================================
//  Libraries
//==============================================================================

#include "FingerDriver.h"
#include "HardwareConfig.h"

#include <Wire.h>
#include <Adafruit_PWMServoDriver.h>

//==============================================================================
//  Constants and Macro Definitions
//==============================================================================

#define SERVO_MIN  (150)
#define SERVO_MAX  (450)
#define SERVO_FREQ (50)

const int JOINT_STATE_MAX[__NUM_JOINTS__] = {165,165,165,165};
const int JOINT_STATE_MIN[__NUM_JOINTS__] = {0,0,0,0};
const int JOINT_STATE_DEFAULT[__NUM_JOINTS__] = {90,75,70,85};

//==============================================================================
//  Private Data Members
//==============================================================================

static int _joints[__NUM_JOINTS__];
static Adafruit_PWMServoDriver servoDriver = Adafruit_PWMServoDriver(&Wire,SERVO_DRIVER_ADDRESS);

//==============================================================================
//  Private Function Prototypes
//==============================================================================

static void _set_servo(int channel, int angle);

//==============================================================================
//  Public Function Implementation
//==============================================================================

void fd_init(void) {

  servoDriver.begin();
  servoDriver.setPWMFreq(SERVO_FREQ);

  delay(10);
}

int fd_reset_all_joint_states(void) {
  int retVal = 0;

  for (int i=0; i<__NUM_JOINTS__; i++ ) {
    retVal += fd_reset_joint_state((JointId_t)(i));
  }

  return retVal;
}

int fd_reset_joint_state(JointId_t jointId) {
  if (jointId < 0 || jointId >= __NUM_JOINTS__) {
    return -1;
  }

  _joints[jointId] = JOINT_STATE_DEFAULT[jointId];
  _set_servo(jointId,_joints[jointId]);

  return 0;
}

int fd_set_joint_state(JointId_t jointId, int value) {
  if (jointId < 0 || jointId >= __NUM_JOINTS__) {
    return -1;
  }

  if (JOINT_STATE_MAX[jointId] < value || JOINT_STATE_MIN[jointId] > value) {
    return -2;
  } else {
    _joints[jointId] = value;
    _set_servo(jointId,value);
    return 0;
  }
}

int fd_get_joint_state(JointId_t jointId) {
  if (jointId < 0 || jointId >= __NUM_JOINTS__) {
    return -1;
  }

  return _joints[jointId];
}

//==============================================================================
//  Private Function Implementation
//==============================================================================

static void _set_servo(int channel, int angle) {
  int pulselength = map(angle, 0, 180, SERVO_MIN, SERVO_MAX);
  servoDriver.setPWM(channel, 0, pulselength);
}

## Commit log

2019-09-16 initial package upload to repo. Basic URDF constructed, fake relaxed-ik driver created
    [base_spacer.stl, finger_hinge.stl, finger_root.stl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]
2019-10-06 adding all current firmware for the finger, will clean up and update later
2019-10-10 major restructure into multi-ros-package repo; worked on updating fake driver
    [base_spacer.stl, finger_hinge.stl, finger_root.stl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]
